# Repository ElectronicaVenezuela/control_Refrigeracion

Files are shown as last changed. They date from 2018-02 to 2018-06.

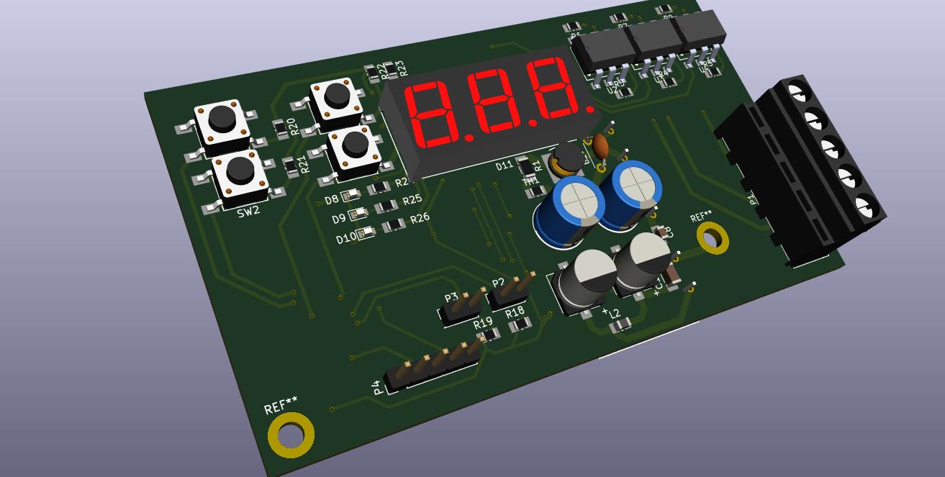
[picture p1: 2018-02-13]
Hartware_2.0.0/FABRICACION/D21_2550.jpg

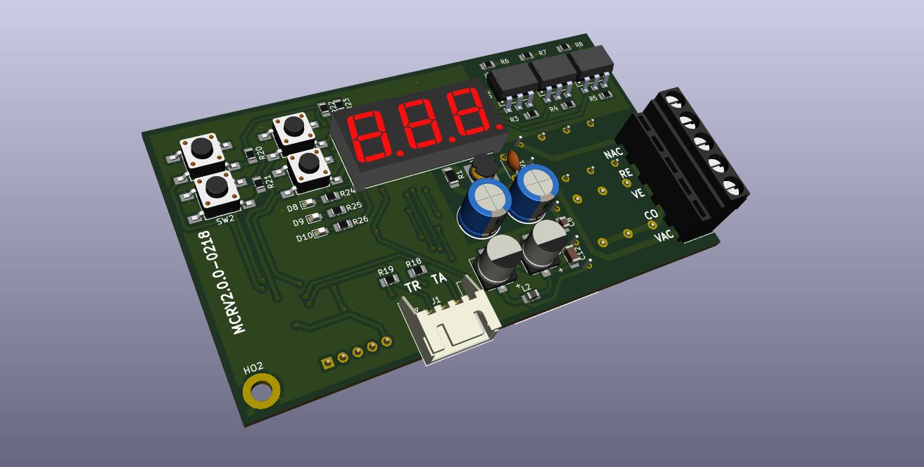
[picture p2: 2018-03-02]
Hartware_2.0.0/doc/D21_2550top.jpg

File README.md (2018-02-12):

# Módulo Control De Refrigeracion Comercial

Tesis para obtar al titulo de ingeniero de la Universidad Nacional Experimental del Táchira (UNET).

## Descripcion

Es un control de refrigeracion comercial con control de ciclos y deshielo, asi como tambien alertas contra posibles anomalias en el sistema de refrigeracion.

## Uso:

 - El hartware fue esta siendo desarrollado en [kicad version Nocturna](http://kicad-pcb.org/download/ubuntu/) para Ubuntu.

 - Las librerias usadas de componentes estan en: 
    -[Symbols](https://github.com/picli3/kicad-symbols.git)
    -[FootPrints](https://github.com/picli3/kicad-footprints.git)
    -[Packages3D](https://github.com/picli3/kicad-packages3D.git)
Se deben clonar y asociarse con el proyecto.

## Autor:

Maykol Rey Maykolrey@gmail.com

## Tutor:

Dr. Cesar contreras.

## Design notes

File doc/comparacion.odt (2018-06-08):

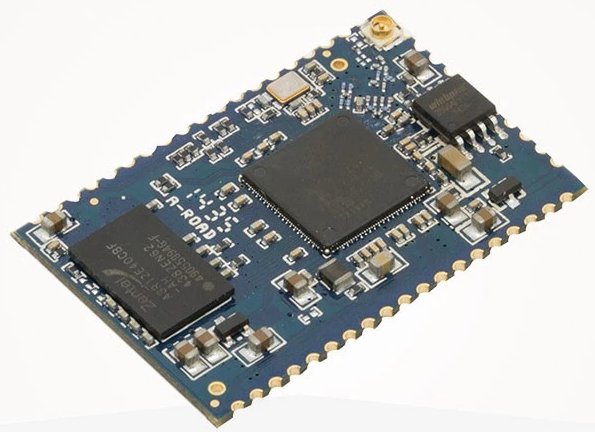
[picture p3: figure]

Comparación de procesadores

Skylab skw72 ar9331 Precio $10

Características

400MHz PCU

1. Conforme a IEEE 802.11b/G/n 1x1wlans

2. DDR2 memoria de hasta 512 MB

Memoria flash de hasta 64 MB

4.4lan puertos y 1 puerto WAN

5. UART de alta velocidad

Soporte técnico de 6. USB 2.0 modo de acogida

7. soporte AP/cliente/modo repetidor

8. soporte UART A WiFi transparente

9. Seguridad: WEP 64/128, WPA, WPA2, TKIP, AES, wapi

10. Conforme cumple los requisitos de medio ambiente

11.40.5 (l) x 27.5 (W) x 2.9 (h) mm Dimensión pequeña

Rasbberry pi zero $24

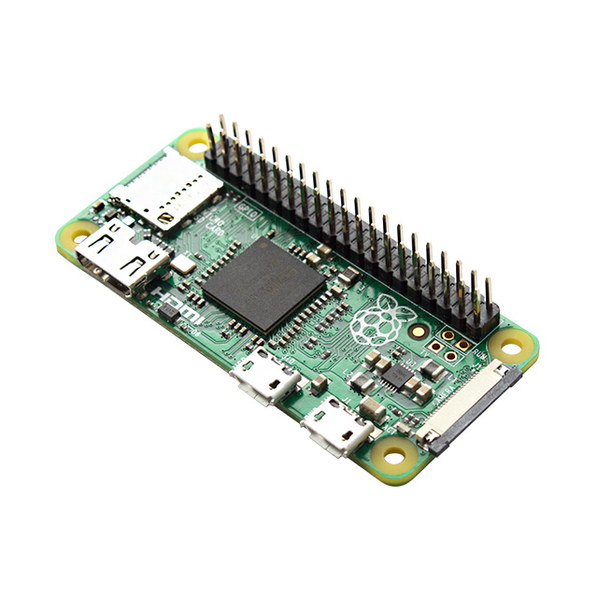
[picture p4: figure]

#### TECHNICAL SPECIFICATIONS

The Raspberry Pi Zero is half the size of a Model A+, with twice the utility. A tiny Raspberry Pi that’s affordable enough for any project!

- 1GHz single-core CPU
- 512MB RAM
- Mini HDMI port
- Micro USB OTG port
- Micro USB power
- HAT-compatible 40-pin header
- Composite video and reset headers
- CSI camera connector (v1.3 only)

### The Omega2 at a Glance $9

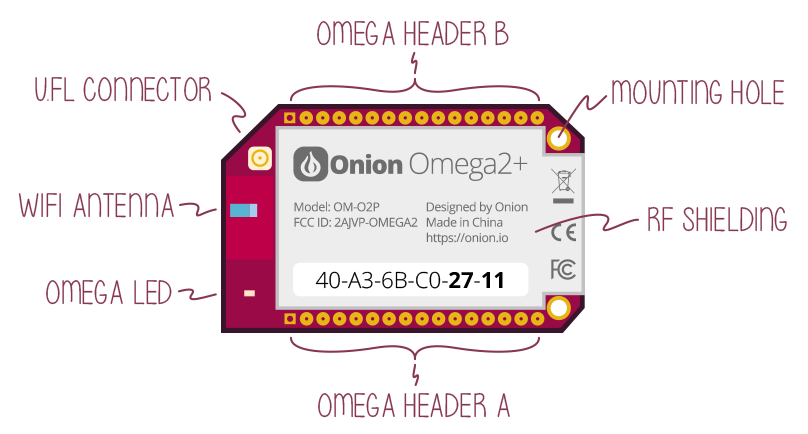
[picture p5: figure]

Omega2+ Specs
Processor | 580MHz MIPS CPU
Memory | 128MB Memory
Storage | 32MB Storage
USB | USB 2.0
MicroSD Slot | Yes
WiFi adapter | b/g/n Wi-Fi
GPIOs | 15
PWM | 2
UART | 2
I2C | 1
SPI | 1
I2S | 1

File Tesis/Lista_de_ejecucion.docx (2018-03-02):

Lista por completar para la tesis

1) fabricar placa a china

2) comprar componentes

3) ensamblar

4) probar algoritmo

5) hacer cubierta e imprimirla.

Documentar.

1) Realizar las cartas y tema el tema legal para realizar la tesis.

2) reestructurar los capitulos I,II y III con las nuevas condiciones.

3) Realizar todo el capitulo IV y V.

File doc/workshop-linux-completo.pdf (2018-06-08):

## Linux embebido

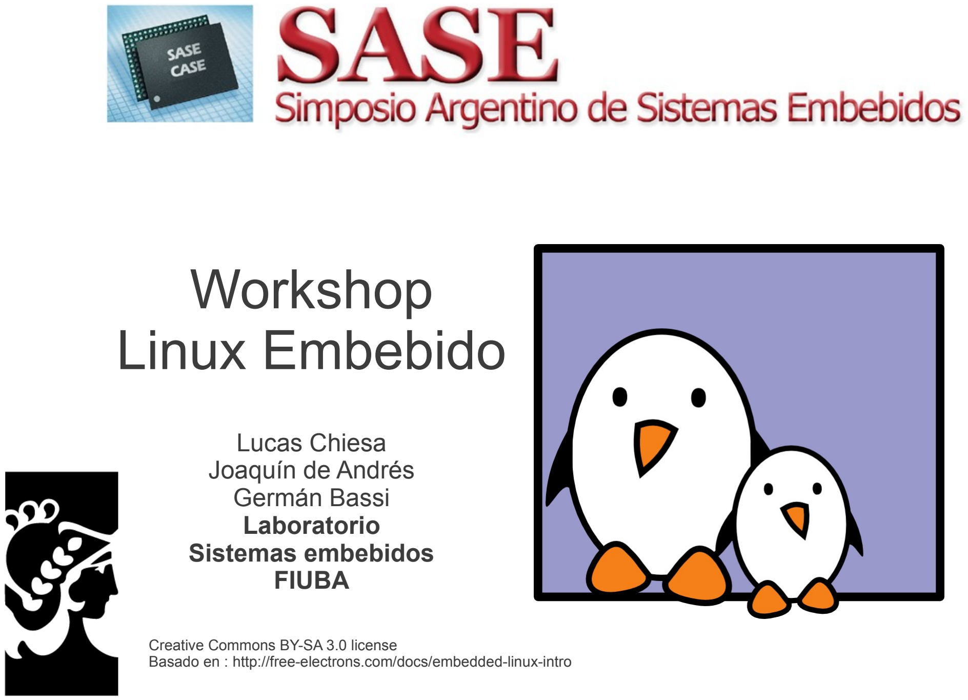
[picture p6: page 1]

## Workshop Linux Embebido

Lucas Chiesa
Joaquín de Andrés
Germán Bassi
Laboratorio
Sistemas embebidos
FIUBA

Creative Commons BY-SA 3.0 license
Basado en : http://free-electrons.com/docs/embedded-linux-intro

SASE 2012 Workshop Linux Embebido | 2

## ¿Sistema embebido?

Un sistema embebido o empotrado es un sistema de computación diseñado para realizar una o algunas pocas funciones dedicadas frecuentemente en un sistema de computación en tiempo real. Los sistemas embebidos se utilizan para usos muy diferentes a los usos generales a los que se suelen someter a las computadoras personales.

Wikipedia, http://es.wikipedia.org/wiki/Sistema_embebido

SASE 2012 Workshop Linux Embebido | 3

## Muchos sistemas diferentes

Es una definición muy genérica:
Cubre muchos tipos diferentes de sistemas
Línea borrosa con sistemas tradicionales
Productos “Consumer Electronics (CE)”:
Routers hogareños, reproductores de DVD, Televisores, cámaras digitales, GPS, celulares ...
Productos industriales:
Controladores de máquinas, alarmas, equipos de vigilancia, autos, satélites...

## Muchos productos diferentes

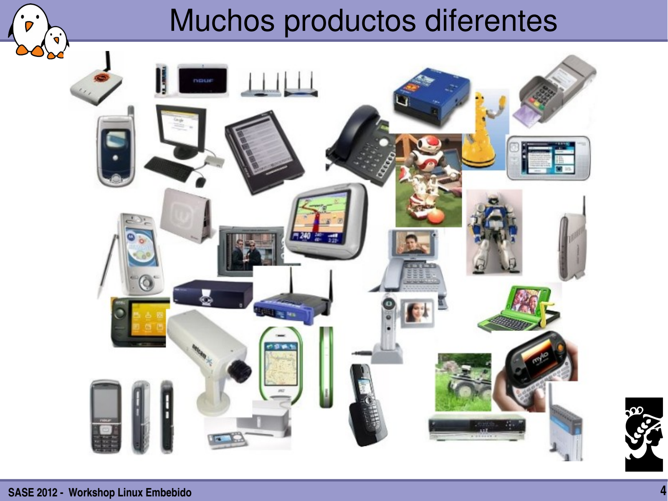
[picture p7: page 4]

SASE 2012 Workshop Linux Embebido | 4

SASE 2012 Workshop Linux Embebido | 5

## Linux embebido

El Software Libre y Abierto ofrece una rango muy amplio de herramientas para desarrollar sistemas embebidos. Ventajas
- Reutilizar componentes existentes para el sistema base. Permite concentrarse en el valor agregado del producto.
- Componentes de alta calidad y muy probados. (Kernel Linux , librerías de C ...)
- Control completo sobre la elección de componentes. Modificaciones posibles ilimitadas.
- Soporte por la comunidades: tutoriales, listas de correo...
- Bajo costo, sin licencias por unidad.
- Acceso más simple al software y a las herramientas.

SASE 2012 Workshop Linux Embebido | 6

## Ejemplos de dispositivos

GPS: TomTom y Garmin
Routers hogareños: Linksys, Netgear PDA: Zaurus, Nokia N8x0
TVs, DVDs: Sony, Philips, ...
Celulares: Motorola, Android, OpenMoko
Y muchos productos que uno no se imagina...

SASE 2012 Workshop Linux Embebido | 7

## Arquitectura global

Hardware

Bootloader

Kernel Linux

Librería de C

Librería | Librería | Librería
Aplicación | Aplicación
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
SASE 2012 Workshop Linux Embebido | 8

## Hardware embebido

El hardware para sistemas embebidos es usualmente diferente de los sistemas comunes.
- Normalmente usan otras arquitecturas:
ARM, MIPS o PowerPC. x86 también es usado.
- Almacenamiento flash (NOR o NAND), usualmente con capacidad limitada. (de pocos MB a cientos de MB)
- Capacidad de RAM limitada (desde unos pocos MB)
- Muchos buses de conexión no comunes en desktops: I2C, SPI, 1-wire, CAN, etc.
Placas de desarrollo por cientos de dolares
- Usualmente usadas como base de nuestro diseño.

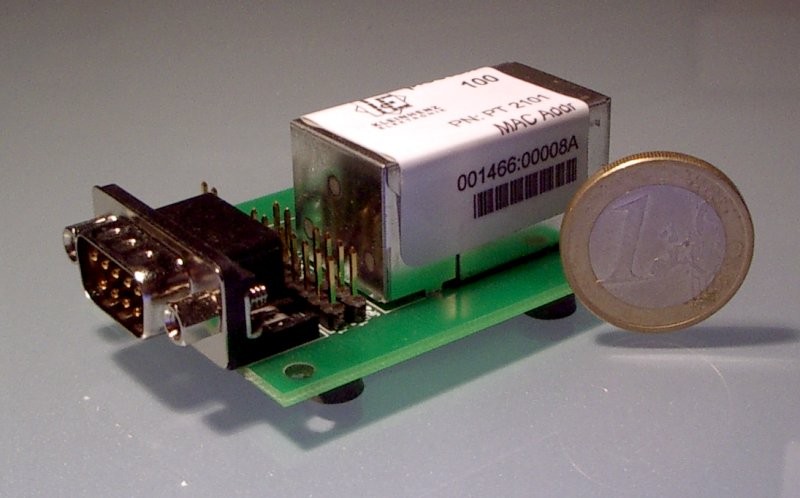
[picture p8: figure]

SASE 2012 Workshop Linux Embebido | 9

## Ejemplos

Picotux 100
ARM7 55 MHz, Netsilicon
NS7520
2 MB de flash
8 MB de RAM
Ethernet
5 GPIOs
Serial

BeagleBoard C4
Cortex A8 750 MHz, TI
OMAP 3550
256 MB de RAM
256 MB de NAND flash
DVI, audio entrada y salida, USB, etc

SASE 2012 Workshop Linux Embebido | 10

## Requerimientos mínimos

Una CPU soportada por el GCC y el Kernel Linux
- 32 bit CPU
- CPUs sin MMU son soportadas por uClinux, que no vamos a ver ahora.
Unos MB de RAM, desde 4 MB.
8 MB para hacer algo útil.
Unos pocos MB de almacenamiento, desde 2 MB.
4 MB para hacer algo útil.
Linux no está diseñado para procesadores con KBs de RAM o ROM:
- Se usan sin SO.
- Sistemas reducidos, como FreeRTOS

SASE 2012 Workshop Linux Embebido | 11

## Componentes de software

Crosscompilation toolchain
- Compilador que se ejecuta en una computadora de desarrollo y genera binarios para el destino.
Bootloader
- Iniciado por el hardware, es el responsable de la inicialización básica y ejecutar el Kernel.
Kernel Linux
- Contiene el administrador de procesos y memoria, stack de red, controladores de dispositivos, provee servicios a las aplicaciones. Librería de C
- Interfaz entre el Kernel y las aplicaciones de usuario.
Librerías y aplicaciones
- Propias o producidas por otros.

SASE 2012 Workshop Linux Embebido | 12

## Armado de un sistema Linux

Se necesitan realizar diferentes tareas para producir un sistema Linux embebido:
Desarrollo del Board Support Package
- Un BSP contiene el bootloader y Kernel con los drivers necesarios para mi hardware destino.
- No es donde nos vamos a centrar.
Integración del sistema
- Integrar todos los componentes, BSP, librerías y aplicaciones utilizadas y las aplicaciones propias para obtener un sistema funcional.
- Propósito de este curso.
Desarrollo de aplicaciones
- Aplicaciones normales de Linux, pero usando librerías especiales.

SASE 2012 Workshop Linux Embebido | 13

## Root filesystem

En un sistema Linux, los sistemas de archivos se “montan” dentro de una jerarquía global de directorios y archivos.
Un sistema particular, el root, se monta como el directorio /.
En sistemas embebidos, este sistema de archivos contiene todos los archivos del sistema.
Por lo tanto, crearlo es una de las tareas principales de la integración de componentes.
El Kernel normalmente se mantiene separado.

Bootloader

Kernel

Root
filesystem

Contenidos de
la Flash

SASE 2012 Workshop Linux Embebido | 14

## Entorno de desarrollo

Dos maneras de desarrollar un sistema Linux:
- Usar soluciones provistas y soportadas por empresas como MontaVista, Wind River o TimeSys. Cada una tiene sus herramientas propias.
- Usar herramientas provistas por la comunidad.
No vamos a promover ninguna empresa en particular, por lo que vamos a usar herramientas de la comunidad.
- Lo importante es entender los conceptos, migrar de herramienta siempre es más fácil.
Desarrollar un sistema Linux requiere usar Linux.
- Las herramientas comunitarias no están disponibles para otras plataformas.
- Entender Linux en el desktop nos va a facilitar el desarrollo de Linux embebido.

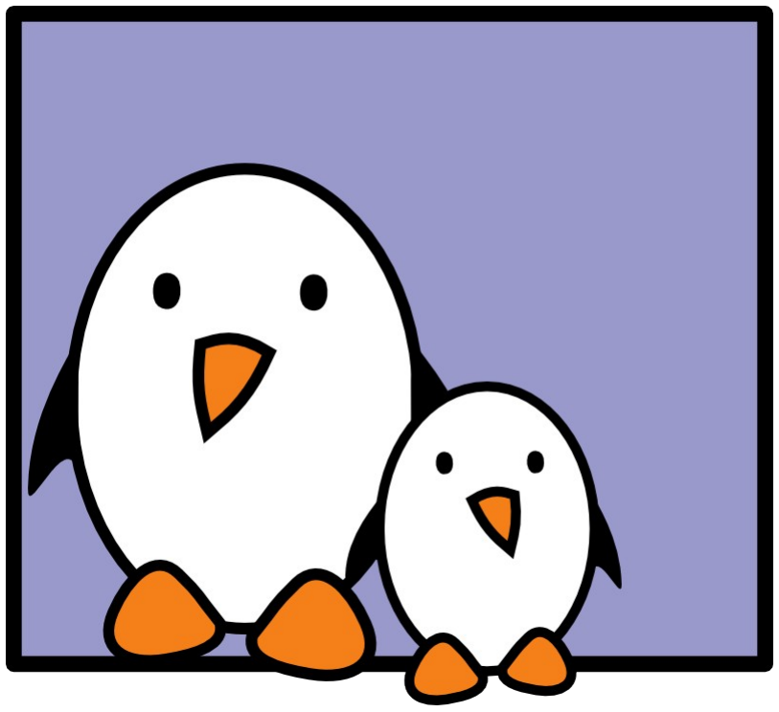
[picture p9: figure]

SASE 2012 Workshop Linux Embebido | 15

## Linux embebido

# Uso de un sistema Linux

SASE 2012 Workshop Linux Embebido | 16

## Uso de un sistema Linux

## Sistema de archivos y dispositivos

SASE 2012 Workshop Linux Embebido | 17

## Creando un sistema de archivos

Ejemplos
mkfs.ext2 /dev/sda1
Formatea la partición /dev/sda1 en formato ext2. mkfs.ext2 -F disk.img
Formatea una imagen de disco en ext2
mkfs.vfat v -F 32 /dev/sda1 (v: verbose) Formatea la misma partición anterior en FAT32.
mkfs.vfat v -F 32 disk.img
Formatea la imagen en FAT32.
Imágenes de discos en blanco se pueden crear así: (archivo de 64 MB): dd if=/dev/zero of=disk.img bs=1M count=64

-F: force. Ejecuta aunque no sea un dispositivo real.

SASE 2012 Workshop Linux Embebido | 18

## Montando un dispositivo

Para hacer cualquier sistema de archivos visible en el sistema hay que montarlos.
La primera vez, se crea el punto de montaje: mkdir /mnt/usbdisk (ejemplo)
Ahora lo montamos:
mount t vfat /dev/sda1 /mnt/usbdisk /dev/sda1: dispositivo físico
t: especifica el formato del sistema de archivo (ext2, ext3, vfat, reiserfs, iso9660...)

Datos
crudos

mount

Estructura
de
directorios

SASE 2012 Workshop Linux Embebido | 19

## Montando un dispositivo

También se puede montar una imagen de un sistema de archivos guardada en un archivo regular (loop devices)
Muy útil para desarrollar y probar un sistema de archivos que estamos armando para otra computadora.
Útil para acceder a los contenidos de una imagen de CD (iso) sin tener que grabar el disco.
Ejemplo:
mount o loop t vfat usbkey.img /mnt/usbdisk

SASE 2012 Workshop Linux Embebido | 20

## Listando dispositivos montados

Usando el comando mount sin argumentos se obtiene la lista:
/dev/hda6 on / type ext3 (rw,noatime)
none on /proc type proc (rw,noatime)
none on /sys type sysfs (rw)
none on /dev/pts type devpts (rw,gid=5,mode=620) usbfs on /proc/bus/usb type usbfs (rw) /dev/hda4 on /data type ext3 (rw,noatime)
none on /dev/shm type tmpfs (rw)
/dev/hda1 on /win type vfat (rw,uid=501,gid=501) none on /proc/sys/fs/binfmt_misc type binfmt_misc (rw)

SASE 2012 Workshop Linux Embebido | 21

## Desmontando dispositivos

umount /mnt/usbdisk
Termina todas las transacciones pendientes en el dispositivo y lo desmonta.
Para poder desmontar un dispositivo hay que cerrar todos sus archivos abiertos:
- Cerrar todos los programas que usen algún archivo del directorio montado.
- Estar seguro que ningún shell esté abierto en esa partición.
- Se puede usar el comando lsof <mount point> (list open files) para ver todos los archivos abiertos en ese directorio.

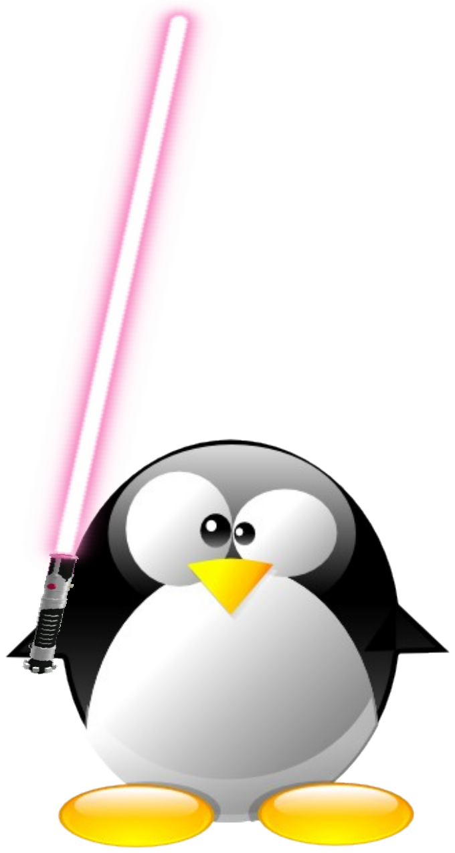
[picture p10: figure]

SASE 2012 Workshop Linux Embebido | 22

## El lado oscuro de root

root: Se necesitan sus privilegios sólo para operaciones específicas, con impacto en la seguridad. Por ejemplo: montar, crear dispositivos, cargar drivers, configurando la red,
cambiar permisos, instalar paquetes...
Por más que uno tenga la clave de root, la cuenta normal tiene que ser suficiente para el 99.9% de las actividades (a menos que seas el sysadmin)
En este curso es aceptable que usen root.
En la vida real, pueden no tener esta cuenta disponible.

SASE 2012 Workshop Linux Embebido | 23

## Usando la cuenta root

En caso que uno realmente quiera ser root...
Si uno tiene el password de root:
su (switch user)
En distribuciones modernas, el comando sudo te da acceso a algunos privilegios de root usando la clave de tu usuario.
Ejemplo: sudo mount /dev/hda4 /home

SASE 2012 Workshop Linux Embebido | 24

## Administración básica del sistema

## Manejo de paquetes

SASE 2012 Workshop Linux Embebido | 25

## Paquetes de software

La forma de distribuir software en GNU/Linux difiere de la que se usa en Windows.
Las distribuciones de Linux proveen una forma central y coherente de instalar, actualizar y borrar aplicaciones y librerías: Paquetes.
Los paquetes contienen la aplicación, las librerías e información extra, como la versión y las dependencias.
- .deb en Debian y Ubuntu, .rpm en Mandriva, Fedora, OpenSUSE Los paquetes se guardan en repositorios, usualmente servers HTTP o FTP.
Siempre hay que usar paquetes oficiales de la distribución, a menos que sea estrictamente necesario.

SASE 2012 Workshop Linux Embebido | 26

## Manejando paquetes de software

Instrucciones para sistemas basados en Debian GNU/Linux: (Debian, Ubuntu...)
Los repositorios de paquetes se especifican en: /etc/apt/sources.list
Para actualizar la lista de paquetes:
sudo aptget update
Para encontrar un paquete para instalar, se pueden usar los buscadores web: http://packages.debian.org o http://packages.ubuntu.com. También se puede usar: aptcache search <keyword>

SASE 2012 Workshop Linux Embebido | 27

## Manejando paquetes de software

Para instalar un paquete:
sudo aptget install <package> Para desinstalar un paquete:
sudo aptget remove <package> Para aplicar todas las actualizaciones: sudo aptget distupgrade
Para obtener información de un paquete: sudo aptcache show <package> Existen interfaces gráficas:
- Synaptic para GNOME
- Adept para KDE
Para más información sobre administración de paquetes: http://www.debian.org/doc/manuals/apthowto/ (http://www.debian.org/doc/manuals/apt-howto/)

SASE 2012 Workshop Linux Embebido | 28

## Apagando el sistema

halt
Apaga inmediatamente el sistema. reboot
Reinicia inmediatamente el sistema.
[Ctrl][Alt][Del]
También funciona el GNU/Linux para reiniciar.
Sistemas embebidos: hay que usar un init y especificar una combinación de teclas en /etc/inittab.

## Práctica – Usando Linux

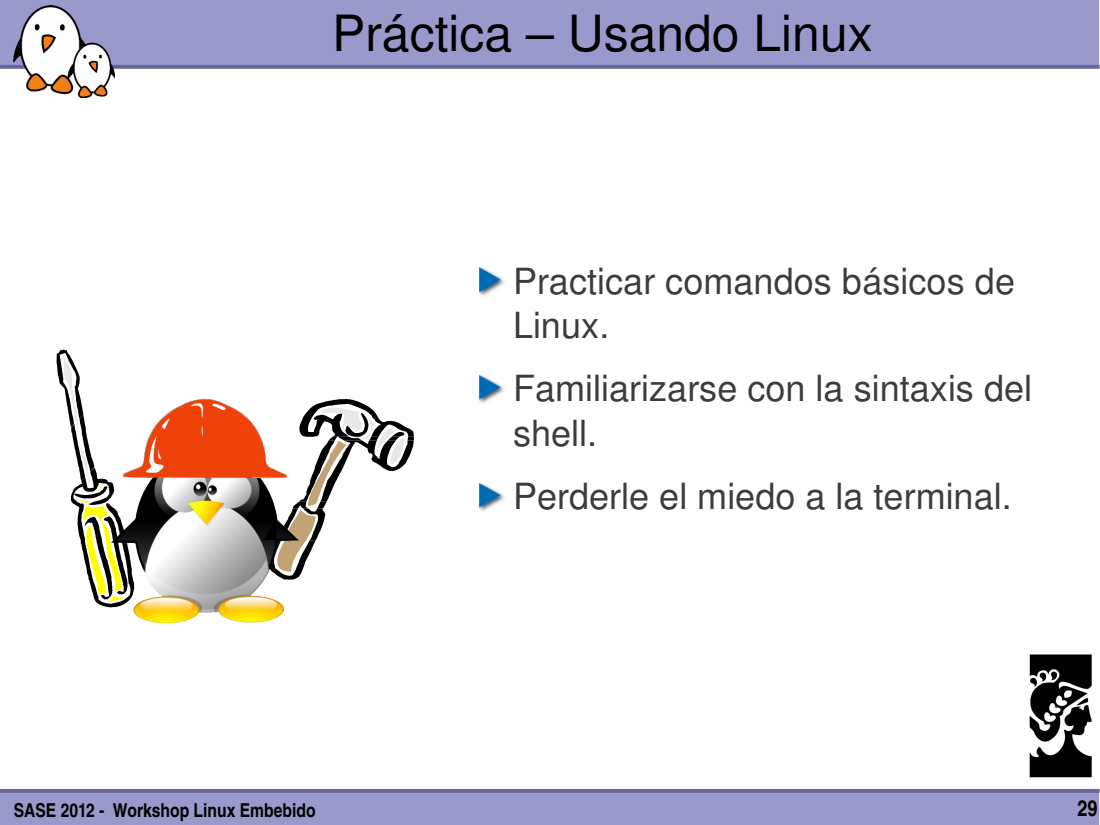
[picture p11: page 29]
SASE 2012 Workshop Linux Embebido

Practicar comandos básicos de
Linux.
Familiarizarse con la sintaxis del
shell.
Perderle el miedo a la terminal.

SASE 2012 Workshop Linux Embebido | 30

## Sistemas embebidos

# Introducción al Kernel Linux

SASE 2012 Workshop Linux Embebido | 31

## Desarrollo de Linux Embebido

## Presentando el kernel

Características de Linux

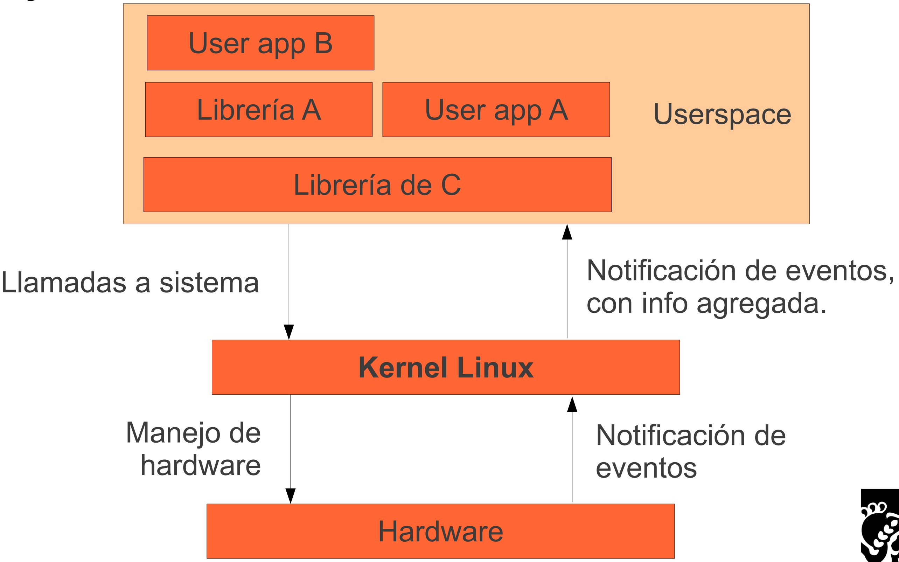
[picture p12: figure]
Userspace; Librería de C; Kernel Linux; Hardware; Librería A; User app A; User app B; Notificación de eventos, con info agregada. Llamadas a sistema; Notificación de eventos; Manejo de hardware

SASE 2012 Workshop Linux Embebido | 32

## Kernel Linux en el sistema

SASE 2012 Workshop Linux Embebido | 33

## Historia

El Kernel Linux es un componente del sistema, requiere librerías y aplicaciones para proveer funcionalidad a los usuarios finales. Creado por un estudiante finlandes, Linus Torvalds, como un hobby en 1991.
- Rápidamente fue adoptado como el Kernel para formar un sistema operativo libre.
Linus Torvalds fue capaz de crear una comunidad de usuarios y programadores grande y dinámica alrededor de Linux. Actualmente cientos de personas contribuyen a cada release del Kernel, tanto individuos particulares como pertenecientes a grandes empresas.

SASE 2012 Workshop Linux Embebido | 34

## Licencia de Linux

Todas las fuentes del Kernel son software libre, liberado bajo la licencia GNU General Public License version 2 (GPL v2).
Para el Kernel, esto implica que:
- Cuando uno recibe o compra un dispositivo con Linux dentro, debe recibir las fuentes de Linux, con todos los derechos de estudiar modificar y redistribuir.
- Cuando uno produce equipos basados en Linux, uno debe dar las fuentes al destinatario, sin restricciones. Más adelante vamos a ver en detalle las licencias libres.

SASE 2012 Workshop Linux Embebido | 35

## Características principales

Portabilidad y soporte de
hardware. Corre en la
mayoría de las arquitecturas. Escalabilidad.
Funciona en super
computadoras como en
pequeños dispositivos.
(4 MB de RAM es suficiente). Cumple con estándares de
interoperatividad
Muy completo y robusto
soporte de red.

Seguridad
No puede ocultar las fallas. El código es revisado por muchos expertos.
Estable y confiable.
Modular. Puede incluir sólo lo que nuestro sistema necesita. Fácil de programar. Se puede aprender de código existente. Muchos recursos en Internet

SASE 2012 Workshop Linux Embebido | 36

## Arquitecturas soportadas

Para el Kernel 2.6.31
Revisar el directorio arch/ (http://lxr.free-electrons.com/source/arch/) en las fuentes.
Requerimiento mínimo: 32 bits, con o sin MMU, y soporte de gcc. Arquitecturas de 32 bits
arm, (http://lxr.free-electrons.com/source/arch/arm/) avr32, (http://lxr.free-electrons.com/source/arch/avr32/) blackfin, (http://lxr.free-electrons.com/source/arch/blackfin/) cris, (http://lxr.free-electrons.com/source/arch/cris/) frv, (http://lxr.free-electrons.com/source/arch/frv/) h8300, (http://lxr.free-electrons.com/source/arch/h8300/) m32r, (http://lxr.free-electrons.com/source/arch/m32r/) m68k, (http://lxr.free-electrons.com/source/arch/m68k/) m68knommu, (http://lxr.free-electrons.com/source/arch/m68knommu/) microblaze, (http://lxr.free-electrons.com/source/arch/microblaze/) mips, (http://lxr.free-electrons.com/source/arch/mips/) mn10300, (http://lxr.free-electrons.com/source/arch/mn10300/) parisc, (http://lxr.free-electrons.com/source/arch/parisc/) s390, (http://lxr.free-electrons.com/source/arch/s390/) sparc, (http://lxr.free-electrons.com/source/arch/sparc/) um, (http://lxr.free-electrons.com/source/arch/um/) xtensa (http://lxr.free-electrons.com/source/arch/xtensa/)
Arquitecturas de 64 bits:
alpha, (http://lxr.free-electrons.com/source/arch/alpha/) ia64, (http://lxr.free-electrons.com/source/arch/ia64/) sparc64 (http://lxr.free-electrons.com/source/arch/sparc64/)
Arquitecturas de 32 o 64 bits:
powerpc, (http://lxr.free-electrons.com/source/arch/powerpc/) x86, (http://lxr.free-electrons.com/source/arch/x86/) sh (http://lxr.free-electrons.com/source/arch/s390/)
Más detalles en: arch/<arch>/Kconfig, arch/<arch>/README, o Documentation/<arch>/

SASE 2012 Workshop Linux Embebido | 37

## Llamadas a sistema

La principal interfaz entre el Kernel y userspace es un conjunto de llamadas a sistema.
Existen ~300 llamadas a sistemas que proveen los servicios principales del Kernel
- Operaciones en archivos y dispositivos, operaciones de red, comunicación entre procesos, administración de procesos, manejo de memoria, timers, threads, sincronización, etc.
Interfaz estable en el tiempo: sólo se pueden agregar nuevas llamadas.
La interfaz a las llamadas al sistema es abstraída por la librería de C. Los programas de userspace usualmente no hacen llamadas al sistema, usan las funciones correspondiente de la librería.

SASE 2012 Workshop Linux Embebido | 38

## Sistemas de archivos virtuales

Linux ofrece información del sistema y el Kernel a userspace mediante sistemas de archivos virtuales (virtuales: no existen en un ningún almacenamiento real). No se necesita saber programar para acceder a esta información!
Montar /proc:
sudo mount t proc none /proc
Montar /sys:
sudo mount t sysfs none /sys
Tipo de fs | Dispositivo o imagen de fs En el caso de un fs virtual cualquier texto es válido
Lugar de montaje

SASE 2012 Workshop Linux Embebido | 39

## Detalles de /proc

Algunos ejemplos:
/proc/cpuinfo: información del procesador /proc/meminfo: estado de la memoria
/proc/version: información de compilación y versión del kernel
/proc/cmdline: línea de comando del Kernel /proc/<pid>/environ: entorno de ejecución /proc/<pid>/cmdline: linea de comando del proceso ... y mucho más! Véalo con sus propios ojos!
Muchos detalles acerca de /proc disponibles en: Documentation/filesystems/proc.txt (http://free-electrons.com/kerneldoc/latest/filesystems/proc.txt)
(casi 2000 líneas) en las fuentes del Kernel.

SASE 2012 Workshop Linux Embebido | 40

## Desarrollo de Linux Embebido

## Kernel Linux

Esquema de versiones y modelo de desarrollo

SASE 2012 Workshop Linux Embebido | 41

## Hasta 2.6

Una nueva rama estable cada 2 o 3 años
- Identificada por un número par en el medio
- Ejemplos: 1.0, 2.0, 2.2, 2.4
Una rama de desarrollo para integrar nueva funcionalidad y cambios mayores
- Identificada por un número impar en el medio
- Ejemplos: 2.1, 2.3, 2.5
- Después de un tiempo, la rama de desarrollo pasaba a ser la base de una rama estable.
Versiones menores de vez en cuando: 2.2.23, 2.5.12, etc.

SASE 2012 Workshop Linux Embebido | 42

## Hasta 2.6

2.4.0 | 2.4.1 | 2.4.2 | 2.4.3 | 2.4.4 | 2.4.5 | 2.4.6 | 2.4.7 | 2.4.8
2.5.0 2.5.1 2.5.2 2.5.3 2.5.4 | 2.6.0 2.6.1

Versión estable

Desarrollo | Estable

Nota: En realidad existen muchas más versiones menores en cada rama.

SASE 2012 Workshop Linux Embebido | 43

## Cambios desde Linux 2.6

Desde 2.6.0, los programadores pudieron agregar muchas nuevas funciones de a una a paso constante sin tener que hacer grandes cambios en los subsistemas existentes. Abrir una nueva rama de desarrollo Linux 2.7 (o 2.9) va a ser necesario cuando Linux 2.6 no pueda acomodar más funciones importantes sin cambios muy grandes.
Gracias a esto, muchas nuevas funciones llegan a los usuarios a un paso mucho más rápido.

SASE 2012 Workshop Linux Embebido | 44

## Cambios desde Linux 2.6

Desde 2.6.14, los programadores del Kernel se pusieron de acuerdo en el siguiente modelo de desarrollo:
Después de un release de una versión 2.6.x, se abre una ventana de 2 semanas para merge durante la cual los principales cambios son aplicados.
Se cierra la ventana de merge con el release de la versión 2.6.(x+1)rc1
Se abre el período para arreglar bugs, de 6 a 10 semanas.
En intervalos regulares durante el período de arreglo de bugs se liberan las versiones de prueba 2.6.(x+1)rcY.
Cuando se lo considera suficientemente estable,
el Kernel 2.6.(x+1) es liberado, y el proceso vuelve a comenzar.

SASE 2012 Workshop Linux Embebido | 45

## Ventanas de merge y arreglos

Ventana de merge | Arreglar bugs
2.6.21 | 2.6.22-rc1

2.6.22-rc2

2.6.22-rc3 | 2.6.22-rc5
2.6.22-rc4 | 2.6.22
2 semanas | 6 a 10 semanas
2.6.21.1 2.6.21.2 | 2.6.21.3 2.6.21.4 | 2.6.21.5

Actualizaciones con
arreglos de bugs
| | 2.6.22.1

SASE 2012 Workshop Linux Embebido | 46

## Más estabilidad con kernel 2.6

Problema: los arreglos de bugs y seguridad se hacen sólo en la versión más nueva (a lo sumo dos anteriores). Las distribuciones, por supuesto, las aplican en los kernels que están usando.
Algunas personas necesitan tener un Kernel nuevo pero con soporte por un plazo prolongado.
Se puede tener soporte de largo plazo de los proveedores de Linux embebido.
Se puede reutilizar las fuentes del Kernel de las versiones de Ubuntu LTS, o Debian (5 o 3 años de updates gratis). Algunas versiones se mantienen por un tiempo prolongado por kernel.org (Linux 2.6.27 por ejemplo).

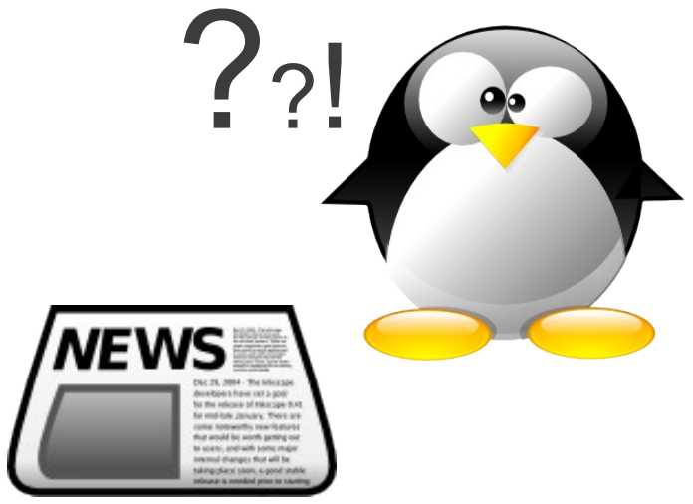
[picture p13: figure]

SASE 2012 Workshop Linux Embebido | 47

## ¿Qué tiene de nuevo cada versión?

¡¡El changelog oficial de cada versión es simplemente una larga lista de parches individuales!!
Muy difícil de saber cuáles son los cambios claves y tener una vista global de los cambios.
Afortunadamente, un resumen de los cambios fundamentales (con suficiente detalle) se encuentra en: http://wiki.kernelnewbies.org/LinuxChanges

commit 3c92c2ba33cd7d666c5f83cc32aa590e794e91b0 Author: Andi Kleen <ak@suse.de>
Date: Tue Oct 11 01:28:33 2005 +0200

[PATCH] i386: Don't discard upper 32bits of HWCR on K8

Need to use long long, not long when RMWing a MSR. I think it's harmless right now, but still should be better fixed
if AMD adds any bits in the upper 32bit of HWCR.

Bug was introduced with the TLB flush filter fix for i386

Signed-off-by: Andi Kleen <ak@suse.de> Signed-off-by: Linus Torvalds <torvalds@osdl.org> ...

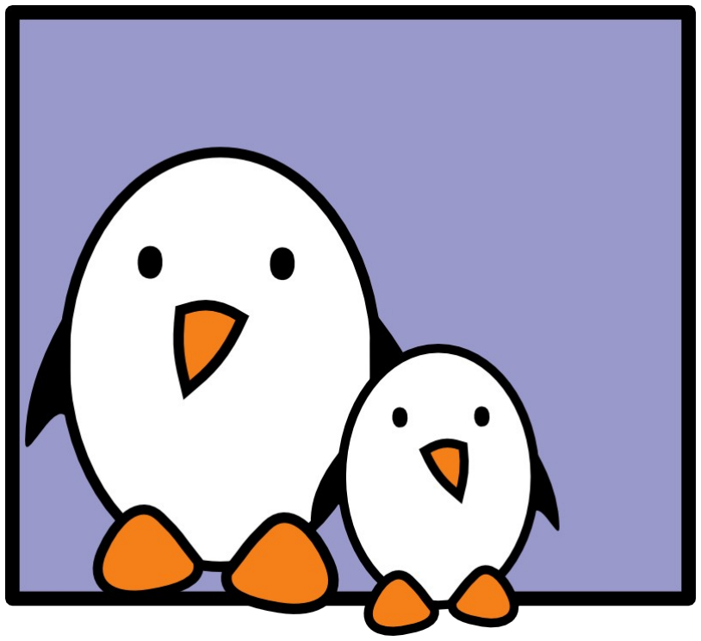
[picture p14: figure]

SASE 2012 Workshop Linux Embebido | 48

## Desarrollo de sistemas Linux

# Crosscompiling toolchains

SASE 2012 Workshop Linux Embebido | 49

## Definición

Las herramientas de desarrollo que uno tiene normalmente en un desktop se llaman toolchain nativo.
Este toolchain corre en el desktop y genera código para el desktop. Usualmente x86.
Para sistemas embebidos usualmente no se puede o no es deseable.
- El target tiene recursos limitados (poca RAM y almacenamiento)
- El target es mucho más lento que el desktop.
- Uno puede no querer tener instalados las herramientas de desarrollo en el target.
Por lo tanto, generalmente se usan crosscompiling toolchains. Corren en el desktop y general código para el target.

SASE 2012 Workshop Linux Embebido | 50

## Definición

x86

x86 | ARM

Máquina que
compila

Máquina
que ejecuta

Código fuente

Toolchain nativo | Cross-compiling toolchain
Binario x86 | Binario ARM

SASE 2012 Workshop Linux Embebido | 51

## Componentes

Binutils | Kernel headers
Librerías de C/C++ | Compilador GCC

GDB debugger
(opcional)

SASE 2012 Workshop Linux Embebido | 52

## Binutils

Binutils es un conjunto de herramientas para manipular binarios de una determinada arquitectura:
- as, el ensamblador, genera código binario a partir de código assembler
- ld, el linker
- ar, ranlib, genera archivos .a, usados para librerías.
- objdump, readelf, size, nm, strings, para inspeccionar binarios. Herramientas de análisis muy útiles!
- strip, remueve partes de los binarios que no se usan. http://www.gnu.org/software/binutils/
Licencia GPL

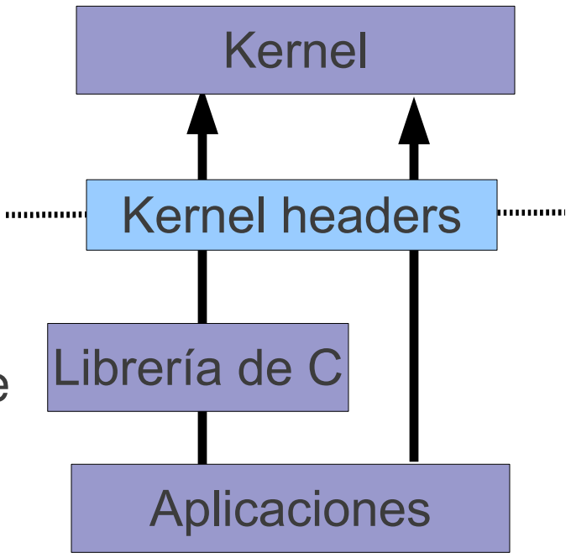
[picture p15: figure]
Kernel; Kernel headers; Librería de C; Aplicaciones

SASE 2012 Workshop Linux Embebido | 53

## Kernel headers

La librería de C y los programas tienen que interactuar con el Kernel
- Llamadas a sistema disponibles.
- Definiciones de constantes.
- Estructura de datos, etc.
Por lo tanto, para compilar la librería de
C se necesitan los Kernel headers, y muchas aplicaciones también.

Disponibles dentro de las fuentes del Kernel

SASE 2012 Workshop Linux Embebido | 54

## Kernel headers

La ABI kerneltouserspace es compatible hacia atrás:
- Binarios generados con un toolchain usando headers anteriores que el Kernel que se está usando, van a funcionar pero no van a poder usar las prestaciones nuevas.
- Binarios compilados contra headers más nuevos que el Kernel en uso pueden romperse si se usan características no presentes en el Kernel viejo.
- No es necesario usar los headers más nuevos, salvo que se necesiten las últimas características.
Los headers se extraen de las fuentes del Kernel con el
comando make headers_install.

SASE 2012 Workshop Linux Embebido | 55

## Compilador GCC

Famoso compilador libre GCC
Puede compilar C, C++, Ada, Fortran, Java, Objective-C, Objective-C++, y generar código para muchas arquitecturas, incluyendo ARM, AVR, AVR32, Blackfin, CRIS, FRV, M32, MIPS, MN10300, PowerPC, SH, v850, i386, x86_64, IA64, Xtensa, etc. http://gcc.gnu.org/
Disponible bajo licencia GPL.
Las librerías que utiliza son LGPL.

SASE 2012 Workshop Linux Embebido | 56

## Librería de C

La librería de C es un componente esencial de una instalación de Linux.
- Interfaz entre las aplicaciones y el Kernel.
- Provee una API de C muy conocida para facilitar el desarrollo de aplicaciones. Existen muchas librerías de C:
glibc, uClibc, eglibc, dietlibc, newlib, etc.
La elección de una librería se debe hacer en el momento de generar el toolchain, ya que el GCC se compila contra la librería.

Kernel

Librería de C

Aplicaciones

SASE 2012 Workshop Linux Embebido | 57

## glibc

http://www.gnu.org/software/libc/
Licencia: LGPL
Librería de C del proyecto GNU.
Diseñada para desempeño, respetar estándares y portabilidad.
Encontrada en casi todos los sistemas GNU / Linux. Por supuesto, mantenida activamente.
Bastante grande para sistemas embebidos: ~ 2.5 MB en arm (version 2.9 libc: 1.5 MB, libm: 750 KB)

SASE 2012 Workshop Linux Embebido | 58

## uClibc

http://www.uclibc.org/ de CodePoet Consulting
Licencia: LGPL
Librería de C pequeña, para sistemas embebidos:
- Muchas opciones de configuración: muchas funciones se pueden activar y desactivar usando la interfaz menuconfig.
- Funciona en Linux/uClinux, en la mayoría de las plataformas embebidas.
- No tiene una ABI estable, depende de la configuración de la librería.
- Se ocupa del tamaño antes que del desempeño.
- Se compila rápido.

SASE 2012 Workshop Linux Embebido | 59

## uClibc

La mayoría de las aplicaciones compilan contra uClibc, y todas las que se usan en embebidos.
Tamaño (arm): 4 veces más chica que glibc!
uClibc 0.9.30.1: ~ 600 KB (libuClibc: 460 KB, libm: 96KB) glibc 2.9: ~ 2.5 MB (para recordar)
Usada en una gran cantidad de dispositivos embebidos, incluidos muchos de “consumer electronics”.
Activamente soportada, gran base de usuarios.
Ahora soportada por MontaVista, TimeSys y Wind River.

SASE 2012 Workshop Linux Embebido | 60

## Querida encojí a los programas

Programa | Usando librerías compartidas | Compilado estático
| glibc | uClibc | glibc | uClibc
Plain “hello world” (stripped) | 5.6 K (glibc 2.9) | 5.4 K (uClibc 0.9.30.1) | 472 K (glibc 2.9) | 18 K (uClibc 0.9.30.1)
Busybox (stripped) | 245 K (older glibc) | 231 K (older uClibc) | 843 K (older glibc) | 311 K (older uClibc)

Comparación de tamaños de ejecutables en ARM

SASE 2012 Workshop Linux Embebido | 61

## eglibc

« Embedded glibc », LGPL
Variante de la GNU C Library (GLIBC) diseñada para funcionar en sistemas embebidos.
Compatible (fuente y binarios) con GLIBC
Sus objetivos incluyen tamaño reducido, componentes configurables, mejor soporte para crosscompilación.
Se puede compilar sin soporte par IPv6, localizaciones y muchas otras funciones.
Soportada por un consorcio, con Freescale, MIPS, MontaVista y Wind River como miembros.
Debian usa eglibc en todas las distribuciones. http://www.eglibc.org

SASE 2012 Workshop Linux Embebido | 62

## Otras librerías de C pequeñas

Existen otras librerías de C más pequeñas, pero ninguna con el objetivo de compilar una gran cantidad de aplicaciones existentes.
Requieren el código escrito especialmente para ellas. Opciones:
- Dietlibc, http://www.fefe.de/dietlibc/. Aproximadamente 70 KB.
- Newlib, http://sourceware.org/newlib/
- Klibc, http://www.kernel.org/pub/linux/libs/klibc/, diseñada para ser usada durante el booteo.

SASE 2012 Workshop Linux Embebido | 63

## Compilando el toolchain

Hay que diferenciar tres máquinas cuando se habla de la creación del toolchain:
- La máquina de compilación, donde el toolchain se compila.
- La máquina host, donde el toolchain se ejecuta.
- La máquina destino, donde se van a ejecutar los binarios generados por el toolchain.
Existen cuatro posibles maneras de crear el toolchain

SASE 2012 Workshop Linux Embebido | 64

## Compilando el toolchain

build | host | target

Nativo
toolchain normal en un desktop
build | host | target

Cross
Genera un toolchain que corre en el desktop y crea código para ejecutarlo en el target
build | host | target

Cross-nativo
Genera un toolchain que corre en el target y genera código para el target
build | host | target

Canadian
Un toolchain que se compila en el desktop, se ejecuta en un server y genera código para el target

La solución más común en embebidos

SASE 2012 Workshop Linux Embebido | 65

## Compilando el toolchain

Hay que tomar muchas decisiones al momento de hacer un toolchain.
- Elegir la librería de C
- Elegir la versión de los componentes que vamos a usar
Y la configuración de todas estas cosas.
- ¿Qué ABI debemos usar? Toolchains para ARM, pueden generar binarios usando la OABI (Old ABI) o la EABI (Embedded ABI), que son incompatibles.
- ¿Debe el toolchain soportar punto flotante por software?, ¿o el hardware provee soporte para estas operaciones?
- ¿Debe el toolchain soportar localización, IPv6, u otras características especiales?

## Compilando el toolchain

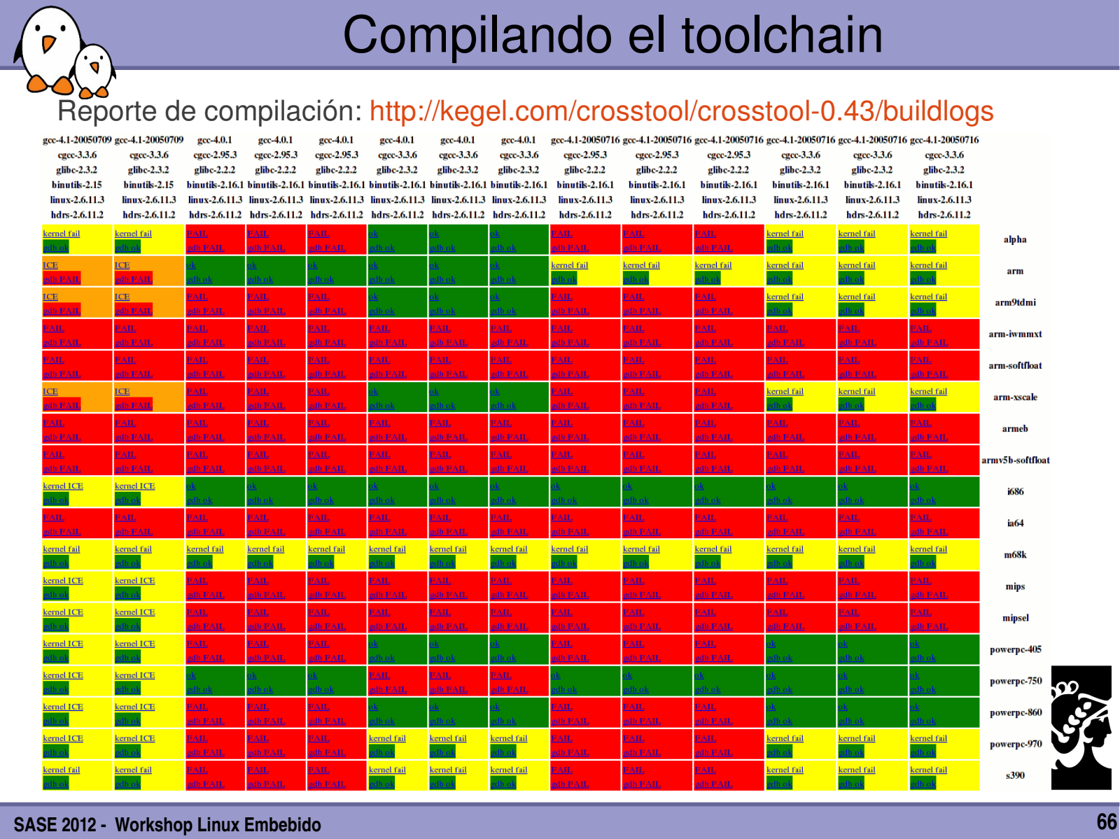
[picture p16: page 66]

SASE 2012 Workshop Linux Embebido | 66

Reporte de compilación: http://kegel.com/crosstool/crosstool-0.43/buildlogs (http://kegel.com/crosstool/crosstool-0.43/buildlogs)

SASE 2012 Workshop Linux Embebido | 67

## Pasos básicos

Extraer e instalar los Kernel headers.
Extraer, configurar, compilar e instalar binutils.
Extraer, configurar y compilar la primera versión del GCC que genera binarios para el target. Lo vamos usar para compilar la librería de C de crosscompilación.
Extraer, configurar y compilar la librería de C con el compilador generado en el paso anterior.
Re configurar y compilar el gcc, contra la nueva librería de
C. Así obtenemos el gcc que vamos a usar.

SASE 2012 Workshop Linux Embebido | 68

## Toolchains caseros

Compilar un cross toolchain a mano es una tarea dolorosa y difícil. Podemos tardar varios días en lograrlo!
Muchos detalles que saber y entender. Muchos componentes que compilar.
Muchas decisiones para tomar.
(configuración de la librería de C para tu plataforma)
Necesitamos fuentes de muchos programas diversos. Estar familiarizado con los problemas actuales del gcc y los parches para tu arquitectura.
Es útil tener práctica compilando programas complejos. http://www.aleph1.co.uk/armlinux/docs/toolchain/toolchHOWTO.pdf ¡Te dice cuán entretenido puede ser!

SASE 2012 Workshop Linux Embebido | 69

## Usar toolchains precompilados

La elección más popular, por ser lo más simple y fácil. Primero, hay que determinar qué toolchain se necesita. CPU, endianism, librería de C, componentes, ABI, punto flotante, etc..
Existen muchos toolchains precompilados:
- CodeSourcery, http://www.codesourcery.com, es una referencia en el área. No te proveen Linux+uClibc.
- Linaro mantiene toolchains optimizados para ARM: https://wiki.linaro.org/WorkingGroups/ToolChain (Linaro contrató a CodeSourcery y agregó cosas)
- Más información en http://elinux.org/Toolchains

SASE 2012 Workshop Linux Embebido | 70

## Usando toolchains precompilados

Seguir las instrucciones provistas por el fabricante. Usualmente es cuestión de descomprimir el archivo y dejarlo en el lugar correspondiente:
- ¡Los toolchains no suelen ser reubicables!
Los tenés que tener en el lugar donde fueron diseñados.
- A partir de gcc 4.x esto no es necesario, pero suele ser lo más común y sencillo.
Finalmente, agregar el toolchain a nuestro PATH:
export PATH=/path/to/toolchain/bin/:$PATH

SASE 2012 Workshop Linux Embebido | 71

## Herramientas para compilar

Otra solución es usar utilidades que automatizan el proceso de creación de un toolchain.
Las mismas ventajas que los precompilados, no hay que meterse con la tediosa compilación manual.
Ofrecen mayor flexibilidad que los toolchains ya compilados. Puedo seleccionar todas las opciones que quiero.
Usualmente incluyen los parches recomendables para los distintos componentes en las distintas arquitecturas.
Son scripts de shell o Makefiles que automatizan el proceso de descargar, extraer, configurar y compilar los distintos componentes.

SASE 2012 Workshop Linux Embebido | 72

Crosstool
- Herramienta original, escrita por Dan Kegel
- Conjunto de scripts y parches, glibconly
- No se mantiene más
- http://www.kegel.com/crosstool
Crosstoolng
- Reescritura de Crosstool, con una sistema de configuración del estilo de menuconfig.
- Más prestaciones: soporta uClibc, glibc, eglibc, hard y soft float, muchas arquitecturas.
- Activamente mantenido.
- http://ymorin.isageek.org/dokuwiki/projects/crosstool (http://ymorin.is-a-geek.org/dokuwiki/projects/crosstool)

## Herramientas para compilar

SASE 2012 Workshop Linux Embebido | 73

## Herramientas para compilar

Muchas herramientas para hacer rootfs también permiten compilar el toolchain.
Buildroot
- Basado en Makefile, sólo uClibc, mantenido por la comunidad. http://buildroot.uclibc.org
PTXdist
- Basado en Makefile, uClibc o glibc, mantenido principalmente por Pengutronix
- http://www.pengutronix.de/software/ptxdist/index_en.html OpenEmbedded
- El sistema de compilación más completo y complejo disponible.
- http://www.openembedded.org/

## Práctica – Usando CrosstoolNG

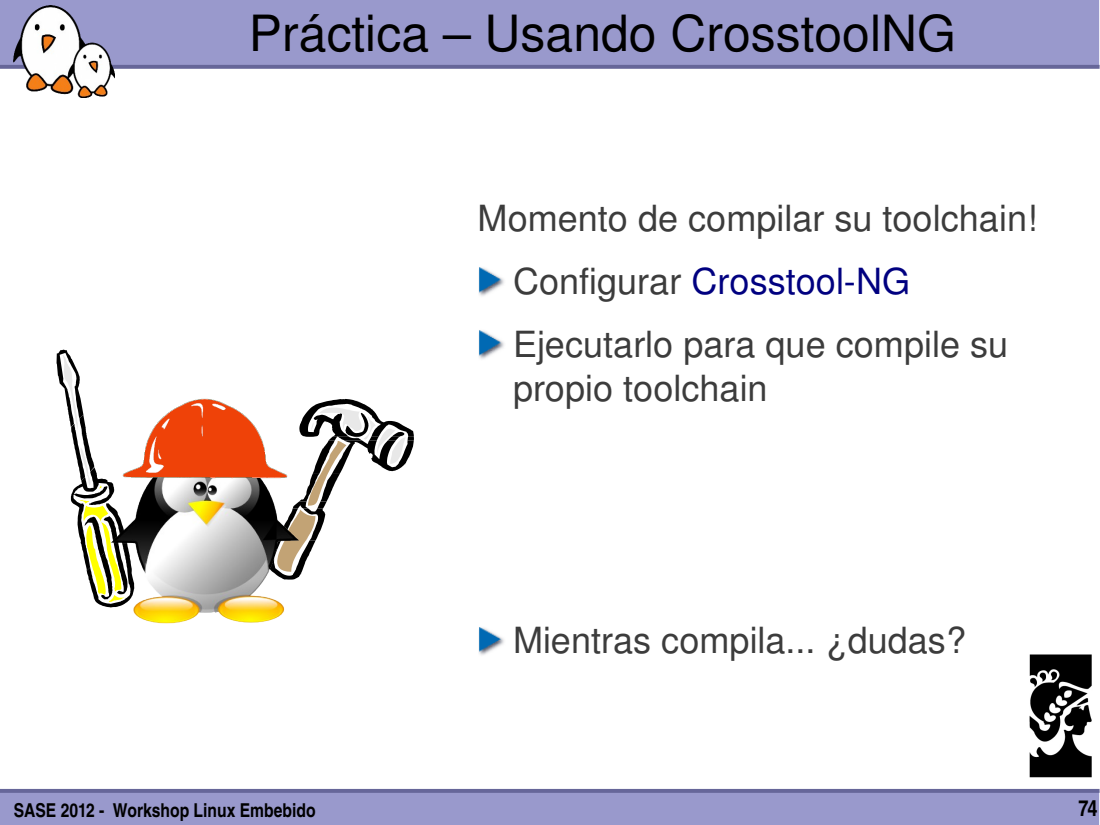
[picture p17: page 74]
SASE 2012 Workshop Linux Embebido

Momento de compilar su toolchain!
Configurar Crosstool-NG
Ejecutarlo para que compile su
propio toolchain

Mientras compila... ¿dudas?

## Linux embebido

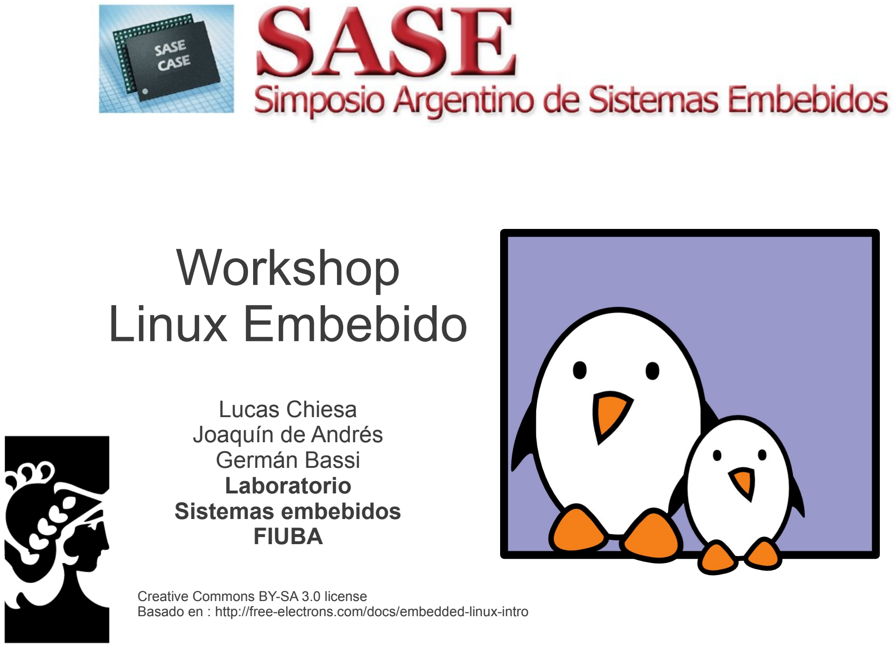
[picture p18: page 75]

## Workshop Linux Embebido

Lucas Chiesa
Joaquín de Andrés
Germán Bassi
Laboratorio
Sistemas embebidos
FIUBA

Creative Commons BY-SA 3.0 license
Basado en : http://free-electrons.com/docs/embedded-linux-intro

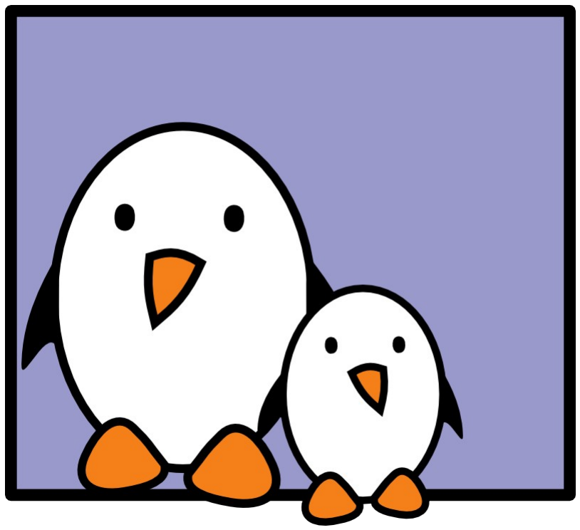
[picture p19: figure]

SASE 2012 Workshop Linux Embebido | 76

## Desarrollo de sistemas Linux

# Bootloaders

SASE 2012 Workshop Linux Embebido | 77

## Bootloaders

El bootloader es un programa responsable de:
- Inicialización básica del hardware.
- Cargar una aplicación binaria, usualmente el Kernel del SO, desde un almacenamiento flash, desde la red, o desde cualquier otro tipo de almacenamiento no volátil.
- Descompresión eventual de la aplicación binaria.
- Ejecución de la aplicación.
Además de las funciones básicas, la mayoría de los bootloaders proveen un shell que implementan diferentes operaciones.
- Inspección de memoria, diagnóstico de hardware, testeo, etc..

SASE 2012 Workshop Linux Embebido | 78

## Bootloaders on x86

Los procesadores x86 son usados típicamente en placas que contienen memoria no volátil donde se encuentra un programa, la BIOS.
El programa es ejecutado desde la CPU después de un reset y es responsable de la inicialización básica del hardware y cargar una pequeña porción de código de almacenamiento no volátil.
- Este código es usualmente los primeros 512 bytes de un disco rígido.
Este código usualmente es la primera etapa del bootloader (1º stage bootloader), que va a cargar el bootloader “real”. Luego, el bootloader puede ofrecer todas sus características. Típicamente entienden sistemas de archivos, para cargar el Kernel directo del FS.

SASE 2012 Workshop Linux Embebido | 79

## Bootloaders on x86

GRUB, Grand Unified Bootloader, es el más poderoso. http://www.gnu.org/software/grub/
- Puede leer muchos sistemas de archivos y cargar el Kernel y su configuración. Provee un shell muy poderoso con muchos comandos. Soporte de red, etc.
LILO, el bootloader original de Linux http://freshmeat.net/projects/lilo/
Syslinux, para bootear de red o de medios http://syslinux.zytor.com

SASE 2012 Workshop Linux Embebido | 80

## Bootloaders en embebidos

En arquitecturas embebidas, el booteo de bajo nivel depende de cada CPU y cada placa.
- Algunas placas tienen una NOR flash de la cual la CPU comienza la ejecución después del reset. En ese caso, el bootloader se debe grabar directamente en la dirección apropiada de esa NOR.
- Algunas CPUs tiene código de booteo integrado en una ROM interna que automáticamente carga una porción de NAND flash en SRAM. En ese caso un bootloader mínimo de primera etapa se debe cargar en ese lugar de NAND. Luego, éste va a cargar el bootloader definitivo en DRAM y ejecutarlo. (BootROM on AT91SAM CPUs, Steppingstone on S3C24xx CPUs, etc.).
El bootloader en embebidos inicia justo después de un reset de la CPU. Debe inicializar todos los dispositivos, incluyendo el controlador de memoria para poder acceder a la DRAM.
Como el proceso de booteo es altamente dependiendo del fabricante es necesario tener la documentación propia del equipo.

SASE 2012 Workshop Linux Embebido | 81

## Bootloaders en embebidos

Nos vamos a centrar en el bootloader principal, por ser el más genérico y por ofrecer la mayor cantidad de prestaciones. Hay varios bootloaders libres genéricos.
Estos son los más populares:
- U-Boot, el “universal bootloader” por Denx
El más usado en ARM, también usado en PPC, MIPS, x86, m68k, NIOS, etc. El estándar defacto actual, y es el que vamos a utilizar. http://www.denx.de/wiki/U-Boot (http://www.denx.de/wiki/U-Boot)
- Barebox, un nuevo bootloader escrito como sucesor a U-Boot. Mejor diseño, mejor código y en desarrollo activo pero todavía no tiene tanto soporte de hardware como U-Boot.
http://www.barebox.org
Hay muchos otros bootloaders, libres y propietarios, usualmente específicos para alguna arquitectura.
- RedBoot, Yaboot, PMON, etc.

SASE 2012 Workshop Linux Embebido | 82

## Desarrollo de sistemas Linux

## Accediendo a una consola serie

SASE 2012 Workshop Linux Embebido | 83

## Minicom

Definición: programa de comunicación serie. Disponible en todas las distribuciones GNU / Linux. Capacidades:
- Consola serie a un sistema Unix remoto
- Transferencia de archivos
- Controlar módems y dialup
- Configuración del puerto serie

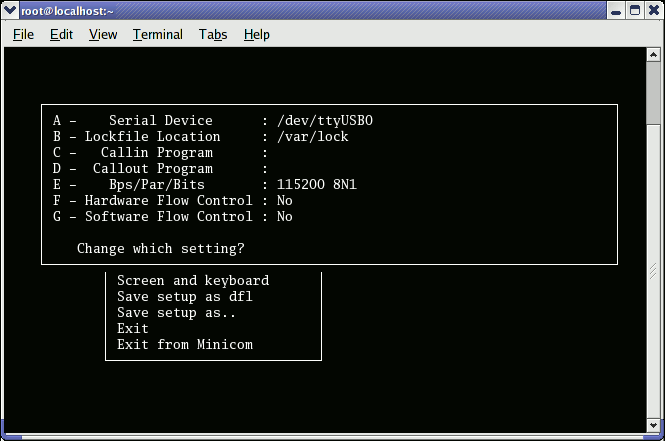
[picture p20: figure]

SASE 2012 Workshop Linux Embebido | 84

## Minicom

Abrirlo ejecutando
minicom s para
configurar minicom
Un poco austero al
principio, pero después
resulta amistoso.

SASE 2012 Workshop Linux Embebido | 85

## Otras terminales series

GTKTerm: http://www.jlsinfo.com/julien/linux/ (http://www.jls-info.com/julien/linux/)
Gráfico. Menos poderoso que Minicom, pero con una interfaz más simple y más atractiva. Disponible en distros recientes. CuteCom: http://cutecom.sourceforge.net/
Otra terminal gráfica amistosa. Disponible en distros recientes. picocom: http://freshmeat.net/projects/picocom/
Emulador muy pequeño (20K), se puede usar embebido
GNU Screen: también se puede usar como terminal serie: screen <device> <baudrate>
Ejemplo:
screen /dev/ttyS0 115200

## Práctica – Bootloaders

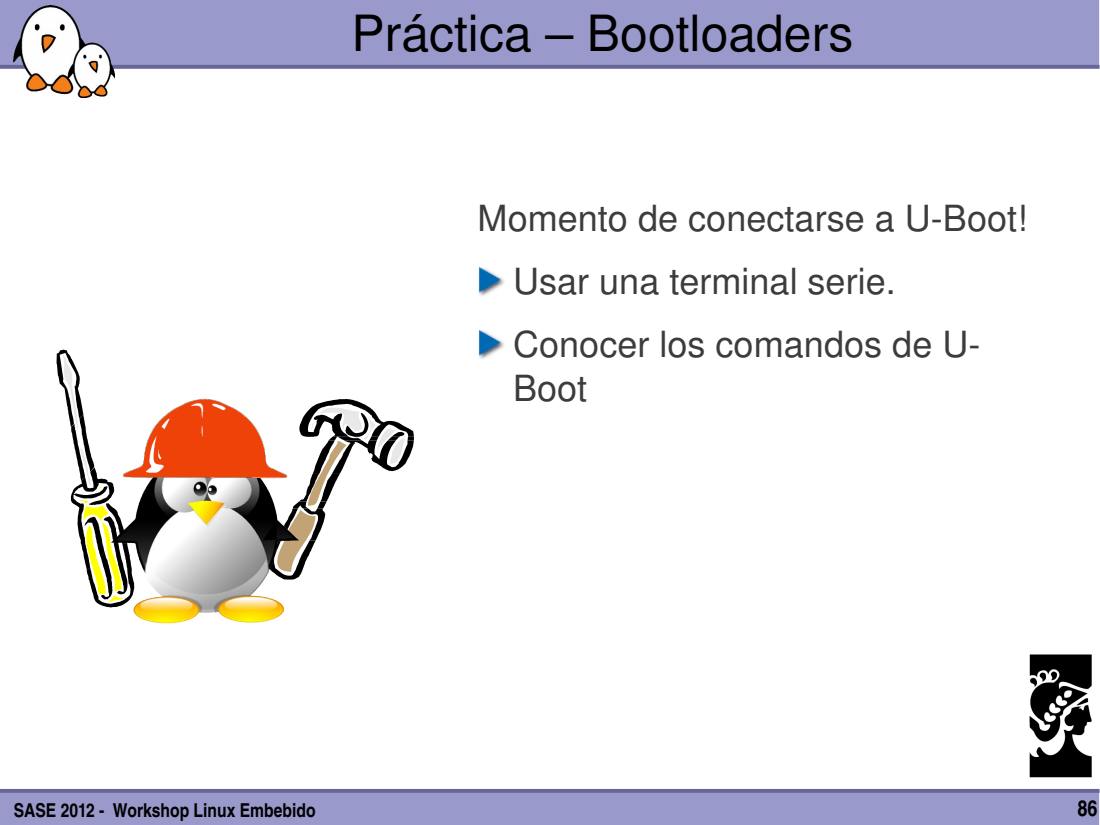
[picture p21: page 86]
SASE 2012 Workshop Linux Embebido

Momento de conectarse a U-Boot!
Usar una terminal serie.
Conocer los comandos de U-
Boot

SASE 2012 Workshop Linux Embebido | 87

## Uso embebido del Kernel Linux

# Uso embebido del Kernel Linux

SASE 2012 Workshop Linux Embebido | 88

## Contenidos

Compilando y booteando
Fuentes del Kernel
Configuración del Kernel
Compilando el Kernel
Inicio del sistema
Archivos de dispositivos
Cross compilando el Kernel

SASE 2012 Workshop Linux Embebido | 89

## Uso embebido del Kernel Linux

## Compilando y Booteando el Kernel

Fuentes del Kernel Linux

SASE 2012 Workshop Linux Embebido | 90

## Fuentes del Kernel

La versión oficial del Kernel, liberada por Linus Torvals, está disponible en http://www.kernel.org
- Esta versión sigue el modelo de desarrollo descripto anteriormente.
- Sin embargo, puede no contener los últimos cambios de un área específica. Algunos cambios pudieron darse después de la ventana de merge o estar todavía en desarrollo.
Muchas subcomunidades del Kernel mantienen sus propias versiones, usualmente con funciones más nuevas y menos estables.
- Comunidades de arquitecturas (ARM, MIPS, PowerPC, etc.), comunidades de drivers (I2C, SPI, USB, PCI, red, etc.), otras comunidades (realtime, etc.)
- Usualmente no liberan versiones oficiales sino que mantienen las ramas de desarrollo.

SASE 2012 Workshop Linux Embebido | 91

## Tamaño del Kernel Linux

Fuentes del Linux 2.6.31:
Tamaño crudo: 350 MB (30,900 archivos, ~ 12,000,000 líneas) gzip: 75 MB
bzip2: 59 MB (mejor)
lzma: 49 MB (el mejor)
Un Linux mínimo 2.6.29 compilado con la opción CONFIG_EMBEDDED, para bootear en un QEMU PC (disco IDE, ext2 filesystem, binarios ELF): 532 KB (comprimido), 1325 KB (descomprimido)
¿Por qué son tan grandes las fuentes?
Proveen miles de drivers, muchos protocolos de red, muchas arquitecturas, muchos sistemas de archivos, etc...
El núcleo de Linux (scheduler, manejador de memoria...) es bastante chico.

SASE 2012 Workshop Linux Embebido | 92

## Tamaño del Kernel Linux

arch
block
crypto
Documentation
drivers
fs
include
init
ipc
kernel
lib
mm
net
scripts
security
sound
usr
0 | 50000 | 100000 | 150000

Tamaño del fuente de Linux por directorios (KB)

Linux 2.6.17
Medido con:
du s apparentsize

SASE 2012 Workshop Linux Embebido | 93

## Bajando las fuentes

Archivos completos
- Contiene las fuentes completas del kernel.
- Bastante para bajar y para descomprimir. Es necesario hacerlo por lo menos una vez.
- Ejemplo: http://kernel.org/pub/linux/kernel/v2.6/linux-2.6.14.7.tar.bz2 Parches incrementales entre versiones
- Asume que tenés una versión base y que aplicaste todos los parches en el orden correcto.
- Rápido para bajar y aplicar
- Ejemplo
http://kernel.org/pub/linux/kernel/v2.6/patch-2.6.14.bz2 (2.6.13 to 2.6.14) http://kernel.org/pub/linux/kernel/v2.6/patch-2.6.14.7.bz2 (2.6.14 to 2.6.14.7)
Todas las versiones anteriores están disponibles en: http://kernel.org/pub/linux/kernel/

SASE 2012 Workshop Linux Embebido | 94

## Aplicando un parche a Linux

Siempre aplicar a la versión x.y.<z-1> Se pueden bajar comprimidos en gzip, bzip2.
Siempre producidos para n=1
Ejemplo:
cd linux-2.6.13
bzcat ../patch-2.6.14.bz2 | patch p1
bzcat ../patch-2.6.14.7.bz2 | patch p1
cd ..; mv linux-2.6.13 linux-2.6.14.7
Mantener el archivo comprimido: Sirve para verificar la firma.
Uno puede ver y editar el archivo sin descomprimirlo usando vim: vim patch-2.6.14.bz2 ((des)compresión on the fly)

Podés hacer patch 30%
más rápido usando sp1
en lugar de p1
(silent)

## Práctica – Fuentes del Kernel

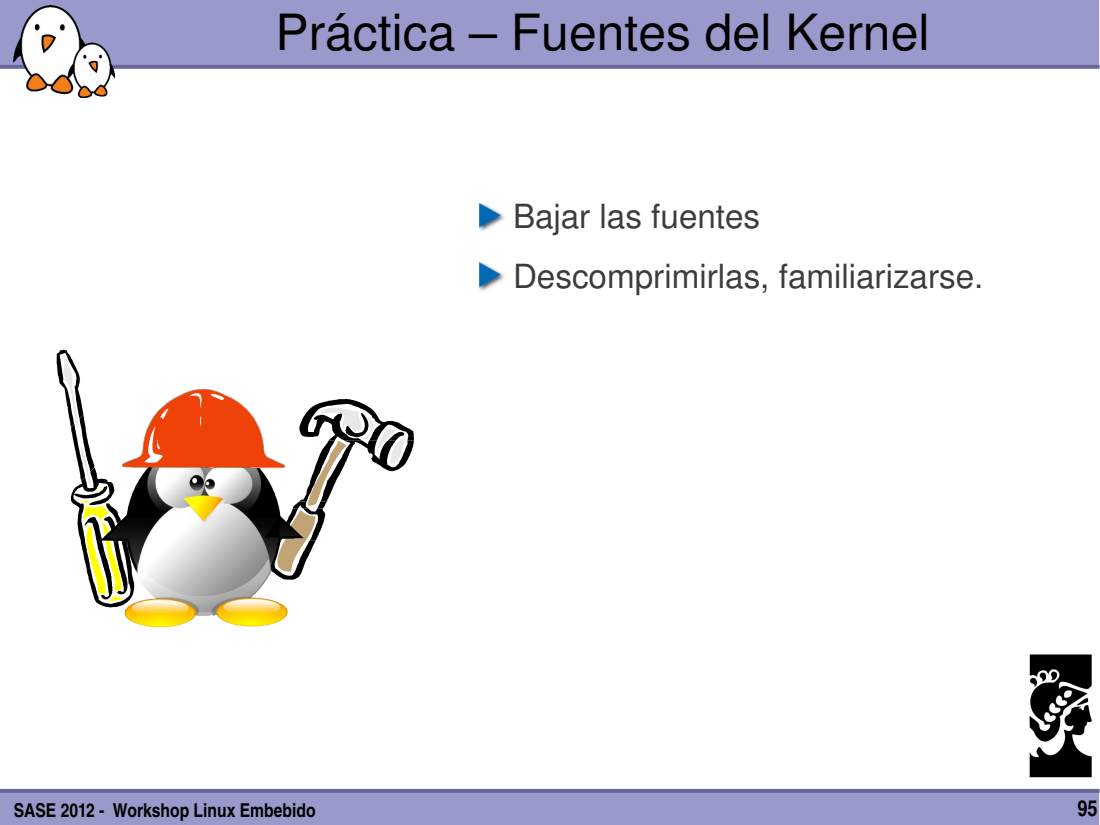
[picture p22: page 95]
SASE 2012 Workshop Linux Embebido

Bajar las fuentes
Descomprimirlas, familiarizarse.

SASE 2012 Workshop Linux Embebido | 96

## Uso embebido del Kernel Linux

## Compilando y booteando

Configuración del Kernel

SASE 2012 Workshop Linux Embebido | 97

## Configuración del Kernel

Ya vimos que el Kernel contiene miles de drivers y otras cosas. Provee miles de opciones para compilar selectivamente diferentes partes del código.
La configuración del Kernel es el proceso de selección de las opciones que queremos que tenga nuestro Kernel
Este conjunto de opciones depende de
- Nuestro hardware
- De las prestaciones que necesitamos del Kernel

SASE 2012 Workshop Linux Embebido | 98

## Configuración del Kernel

La configuración se guarda en el archivo .config en la raíz de las fuentes
- Archivo de texto plano, estilo key=value
Como las opciones tienen dependencias es raro editar el archivo a mano. Se usan interfaces gráficas:
- make [xconfig|gconfig|menuconfig|oldconfig]
- Estos son targets del Makefile del Kernel. Correr make help nos da una lista de targets disponibles.
Para cambiar el Kernel en una distro GNU/Linux:
la configuración usada normalmente está en /boot/, junto con la imagen del Kernel: /boot/config-2.6.17-11-generic

SASE 2012 Workshop Linux Embebido | 99

## make xconfig

make xconfig
La interfaz gráfica más común.
Antes de usar leer:
help > introduction: datos útiles! File browser: facilita cargar archivos de configuración Interfaz de búsqueda de parámetros
Paquetes de Debian / Ubuntu requeridos: libqt3-mtdev, g++

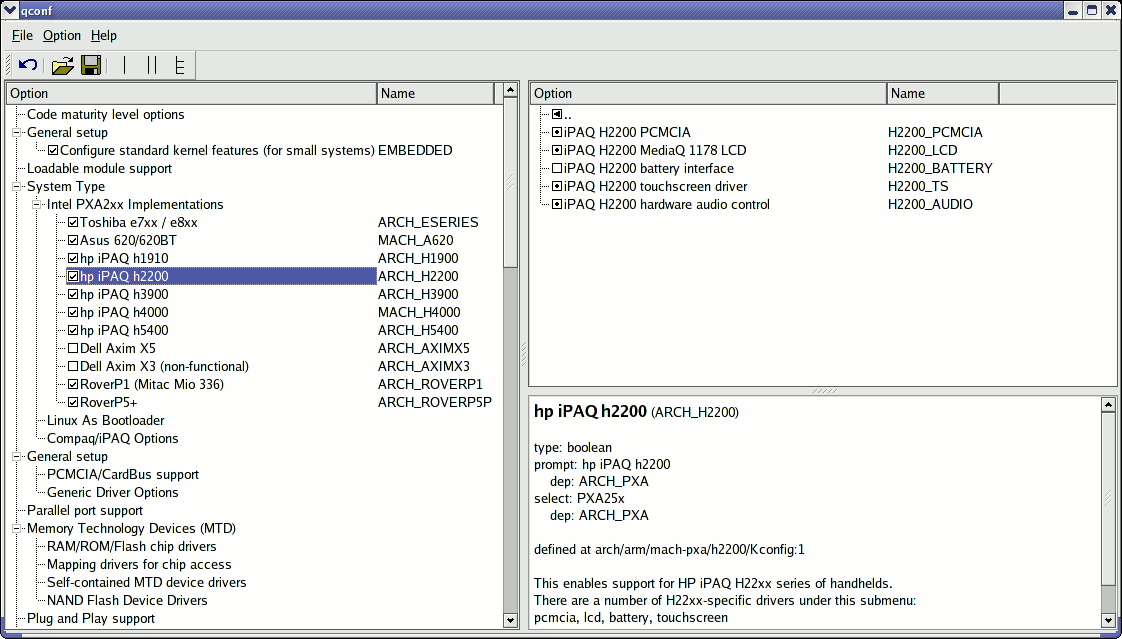
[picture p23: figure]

SASE 2012 Workshop Linux Embebido | 100

## make xconfig screenshot

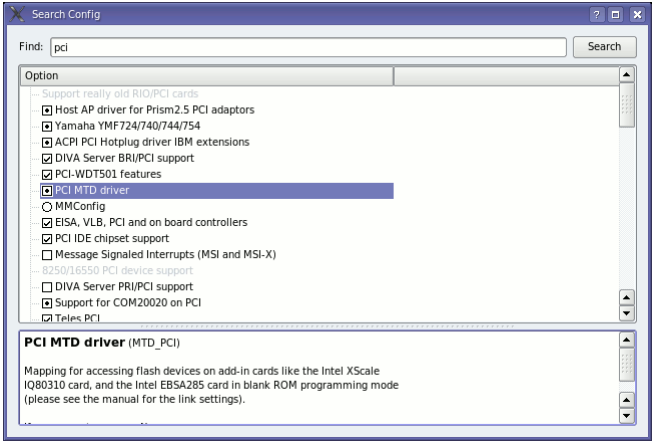
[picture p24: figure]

SASE 2012 Workshop Linux Embebido | 101

## make xconfig: búsqueda

Busca una palabra
cable en las
descripciones
Te deja activar o no
las opciones
encontradas.

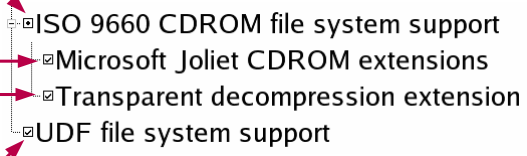
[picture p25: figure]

SASE 2012 Workshop Linux Embebido | 102

## Opciones de configuración

Compilado como módulo (archivo separado) CONFIG_ISO9660_FS=m

Opciones del driver
CONFIG_JOLIET=y
CONFIG_ZISOFS=y

Compilado estático en el Kernel CONFIG_UDF_FS=y

SASE 2012 Workshop Linux Embebido | 103

## .config correspondiente

# CD-ROM/DVD Filesystems

CONFIG_ISO9660_FS=m
CONFIG_JOLIET=y
CONFIG_ZISOFS=y
CONFIG_UDF_FS=y
CONFIG_UDF_NLS=y
# DOS/FAT/NT Filesystems

# CONFIG_MSDOS_FS is not set # CONFIG_VFAT_FS is not set CONFIG_NTFS_FS=m

# CONFIG_NTFS_DEBUG is not set CONFIG_NTFS_RW=y

Nombre de la sección
(ayuda a encontrar settings)

Todos los parámetros comienzan con CONFIG_

SASE 2012 Workshop Linux Embebido | 104

## Dependencias de las opciones

Hay dependencias entre las opciones del Kernel
Por ejemplo, activar un driver de red necesita tener el stack de red compilado.
Dos tipos de dependencias:
- Dependencias “depends on”. En este caso, la opción A que depende de B no es visible hasta que B no esté activada.
- Dependencias “select”. En este caso, si trato de activar la opción A, entonces B es seleccionada automáticamente.
- make xconfig permite ver todas las opciones, incluidas las que no se pueden seleccionar por faltar dependencias. En ese caso, las muestra en color gris.

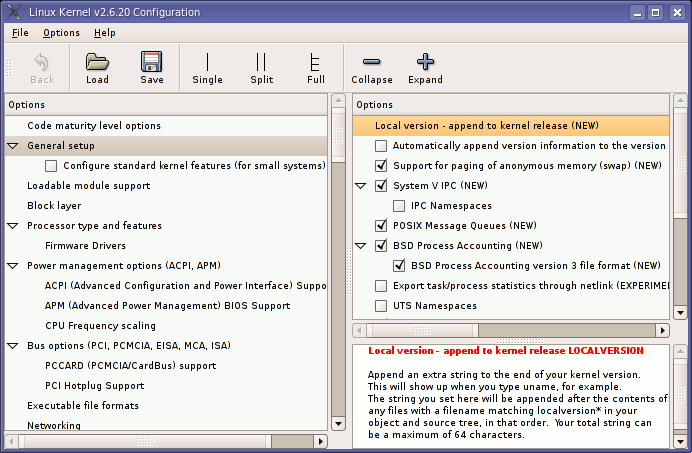
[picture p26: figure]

SASE 2012 Workshop Linux Embebido | 105

## make gconfig

make gconfig
Nuevo frontend basado
en GTK. Funcionalidad
similar a la de make
xconfig.
No se puede buscar.
Paquetes requeridos:
libglade2-dev


SASE 2012 Workshop Linux Embebido | 106

## make menuconfig

make menuconfig
Útil cuando no tengo
interfaz gráfica. Muy
cómoda también!
Misma interfaz que se
usa en otras
herramientas: BusyBox,
buildroot...
Paquetes requeridos:
libncursesdev

SASE 2012 Workshop Linux Embebido | 107

## make oldconfig

make oldconfig
¡Frecuentemente necesario!
Usado para actualizar un archivo .config de una versión anterior del Kernel
Emite advertencias cuando se usaron configuraciones que no existen más en el nuevo Kernel
Pregunta por el valor de nuevas opciones
Si se edita a mano el .config es muy recomendable ejecutar make oldconfig después!

SASE 2012 Workshop Linux Embebido | 108

## make allnoconfig

make allnoconfig
Sólo activa las funciones fuertemente recomendadas Todo lo demás, no lo compila.
Muy útil para partir de lo mínimo y agregar lo que necesitamos.
¡Más fácil agregar lo poco que necesitamos que sacar todo lo que sobra!

SASE 2012 Workshop Linux Embebido | 109

Deshaciendo cambios en la conf.

Un problema frecuente:
Después de varios cambios de configuraciones el Kernel deja de funcionar.
Si uno no se acuerda todos los cambios que fue haciendo, se puede recuperar la configuración anterior: > cp .config.old .config
Todas las interfaces de configuración
(xconfig, menuconfig, allnoconfig...) mantienen una copia de seguridad en .config.old.

SASE 2012 Workshop Linux Embebido | 110

## Configuraciones por arquitectura

El conjunto de configuraciones depende de la arquitectura
- Algunas configuraciones son muy específicas.
- La mayoría de las opciones (opciones globales del Kernel, subsistema de red, filesystems) son visibles en todas las archs. Por omisión, el sistema de compilación asume una compilación nativa.
La arquitectura no se especifica entre las opciones de compilación, sino en un nivel superior.
Vamos a ver cómo seleccionar la arquitectura que queremos.

SASE 2012 Workshop Linux Embebido | 111

## Uso embebido del Kernel Linux

## Compilando e instalando el Kernel Para el sistema host

SASE 2012 Workshop Linux Embebido | 112

## Compilación del kernel

make
- En el directorio principal del código
- Recordar de usar make j n si tenes más de un core n=cores+1
- No tenés que ser root!
Genera
- vmlinux, imagen cruda, sin comprimir en formato ELF, útil para debugging pero no puede ser booteado.
- arch/<arch>/boot/*Image, la imagen final, usualmente comprimida y puede ser booteada.
– bzImage para x86, zImage para ARM, vmImage.gz para Blackfin, etc.
- Los módulos de kernel están distribuidos por todas las fuentes y son archivos que terminan en .ko.

SASE 2012 Workshop Linux Embebido | 113

## Instalación del Kernel

make install
- Instala el Kernel en el sistema host. Se debe correr como root. Instala
- /boot/vmlinuz<version>
La imagen del Kernel comprimida. La misma que en arch/<arch>/boot
- /boot/System.map<version>
Guarda la dirección de los símbolos del Kernel
- /boot/config<version>
Configuración del Kernel para esa versión
- Usualmente ejecuta la utilidad de configuración del bootloader para incorporar el nuevo Kernel

SASE 2012 Workshop Linux Embebido | 114

## Instalación de los módulos

make modules_install
- Instala los módulos en el sistema host. Se debe ejecutar como root. Instala los módulos en /lib/modules/<version>/
- kernel/
Guarda todos archivos los .ko (Kernel Object), manteniendo la estructura de las fuentes.
- modules.alias
Archivo usado por las herramientas que cargan módulos. Por ejemplo:
alias soundservice?-0 snd_mixer_oss
- modules.dep
Dependencias de los módulos
- modules.symbols
Muestra a qué módulo corresponde cada símbolo.


SASE 2012 Workshop Linux Embebido | 115

## Limpiando la fuentes

Limpiar los archivos generados por compilación (para forzar a compilar todo nuevamente):
make clean
Borra todos los archivos generados. Usado cuando cambiamos de arquitectura
Cuidado: también borra el archivos .config! make mrproper
También borrar los archivos de backup y archivos generados por patch. Útil cuando se está haciendo un parche.
make distclean

SASE 2012 Workshop Linux Embebido | 116

## Uso embebido del Kernel Linux

## Compilando y booteando Linux

Archivos de dispositivos

SASE 2012 Workshop Linux Embebido | 117

## Dispositivos de caracteres

Se acceden como un flujo secuencial de caracteres individuales
Se identifican por el tipo c
(ls l):
crwrw 1 root uucp | 4, 64 Feb 23 2004 /dev/ttyS0
crww 1 jdoe tty 136, | 1 Feb 23 2004 /dev/pts/1
crw 1 root root 13, 32 Feb 23 2004 /dev/input/mouse0
crwrwrw 1 root root | 1, | 3 Feb 23 2004 /dev/null
Ejemplos: teclados, mouse, puerto paralelo, IrDA, Bluetooth port, consolas, terminales, etc...

SASE 2012 Workshop Linux Embebido | 118

## Dispositivos de bloques

Se acceden por bloques de datos de algún tamaño fijo. Pueden ser leídos en cualquier orden.
Se identifican por el tipo de archivo b (ls l):
brwrw | 1 root disk | 3, | 1 Feb 23 2004 hda1
brwrw | 1 jdoe floppy | 2, | 0 Feb 23 2004 fd0
brwrw | 1 root disk | 7, | 0 Feb 23 2004 loop0
brwrw | 1 root disk | 1, | 1 Feb 23 2004 ram1
brw | 1 root root | 8, | 1 Feb 23 2004 sda1
Ejemplos: discos rígidos y floppy, discos ram, dispositivos loop...

SASE 2012 Workshop Linux Embebido | 119

## Números minor y major

Como se ve en los ejemplos anteriores los archivos tienen dos números asociados:
El primero: el número major
El segundo: el número minor
Los números major y minor son números usados por el Kernel para vincular un driver con un dispositivo. Los nombres de los archivos no le importan al Kernel! Para saber a qué driver corresponde cada número, ver Documentation/devices.txt. (http://free-electrons.com/kerneldoc/latest/devices.txt)

SASE 2012 Workshop Linux Embebido | 120

## Creación de los archivos

No se crean cuando se carga el driver
Deben ser creados de antemano:
sudo mknod /dev/<device> [c|b] <major> <minor> Ejemplos:
sudo mknod /dev/ttyS0 c 4 64
sudo mknod /dev/hda1 b 3 1

## Práctica – Configurar y compilar

SASE 2012 Workshop Linux Embebido

Configurar su Kernel
Compilarlo
Bootearlo en una máquina virtual

SASE 2012 Workshop Linux Embebido | 122

## Uso embebido del Kernel Linux

## Compilando y booteando Linux

Inicio general del sistema

SASE 2012 Workshop Linux Embebido | 123

## Secuencia de booteo tradicional

Bootloader
Ejecutado por el hardware desde una posición fija de ROM / Flash Inicializa el soporte de los dispositivos donde se encuentra el kernel. (almacenamiento, red, medios removibles)
Carga el Kernel en RAM
Ejecuta la imagen del Kernel (con unos parámetros determinados)
Kernel
Se auto descomprime
Inicializa el núcleo del Kernel y drivers compilados estáticos (necesarios para acceder al root filesystem)
Monta el root filesystem (especificado por el parámetro root)
Ejecuta el primer programa de userspace (especificado por el parámetro init)
Primer programa de userspace
Configura userspace y continúa levantando servicios

SASE 2012 Workshop Linux Embebido | 124

## Parámetros del Kernel

El Kernel acepta parámetros al momento de bootear
Son parte de la configuración del bootloader
Son copiados a RAM por el bootloader a la posición de RAM donde los espera el Kernel.
Útiles para modificar el comportamiento del Kernel al momento de booteo, sin recompilarlo.
Útiles para hacer inicialización avanzada de drivers y el Kernel sin la necesidad de tener complejos scripts de userspace.

SASE 2012 Workshop Linux Embebido | 125

## Ejemplo de los parámetros

HP iPAQ h2200 PDA ejemplo:
root=/dev/ram0 \ | Root fs (primer ramdisk)
rw \ | Modo de montaje del root fs
init=/linuxrc \ | Primer programa userspace
console=ttyS0,115200n8 \ | Consola (serie)
console=tty0 \ | Otra consola (framebuffer)
ramdisk_size=8192 \ | Otros parámetros...
cachepolicy=writethrough
Cientos de parámetros descriptos en: Documentation/kernelparameters.txt (http://free-electrons.com/kerneldoc/latest/kernel-parameters.txt)

SASE 2012 Workshop Linux Embebido | 126

## Desventajas

Se asume que todos los drivers necesarios para montar el root fs (almacenamiento y fs) están compilados estáticos en el kernel. Se puede asumir en la mayoría de los sistemas embebidos que esto va a pasar, donde el hardware es conocido y el kernel está afinado al sistema.
Es usualmente errónea en los sistemas desktop y servers donde una imagen tiene que levantar en una cantidad de dispositivos muy grande.
- Se necesita más flexibilidad
- Los módulos te dan esta flexibilidad, pero no están disponibles hasta montar el root filesystem.
- Necesidad de soportar sistemas complejos (RAID, NFS, etc.)

SASE 2012 Workshop Linux Embebido | 127

## Solución

Una solución es incluir un pequeño rootfs temporal con los módulos necesarios dentro del Kernel mismo. Este sistema de archivos se llama initramfs.
El initramfs es un sistema de archivos comprimido cpio con un rootfs muy básico.
- Un cpio es como un zip pero con un formato mucho más simple. Los scripts del initramfs van a detectar el hardware, cargar los módulos necesarios y montar el rootfs real.
Finalmente, el los scripts del initramfs van a correr la aplicación init del rootfs real y continuar el booteo usual.
Esta técnica reemplaza completamente los init ramdisks (initrds), que se usaban con Linux 2.4, pero no son más necesarios.

SASE 2012 Workshop Linux Embebido | 128

## Secuencia de booteo con initramfs

Bootloader
Ejecutado por el hardware desde una posición fija de ROM / Flash
Inicializa el soporte de los dispositivos donde se encuentra el kernel. (almacenamiento, red, medios removibles)
Carga el Kernel en RAM
Ejecuta la imagen del kernel (con unos parámetros determinados

Kernel
Se descomprime
Inicializa el núcleo y los drivers compilados estáticos.
Descomprime el archivo cpio del initramfs. (si existe, dentro del kernel, sino el bootloader lo copia a una parte específica de memoria) y lo extrae en el cache del kernel.
Si encontró un initramfs, ejecuta el primer programa dentro del initramfs. /init

Userspace: script /init (es lo mismo que un userspace normal)
Corre comandos para configurar el dispositivo
(configuración de red, montar /proc y /sys...)
Monta el rootfs. Cambiar a ese filesystem (switch_root)
Corre /sbin/init

Userspace: /sbin/init
Configura lo que no esté configurado por el initramfs.
Levanta los servicios (demonios, servers) y programas de usuario

Sin

c

a

m

bio

s

SASE 2012 Workshop Linux Embebido | 129

## Ventajas initramfs

Es una solución simple, meter un rootfs directo en el kernel o copiado por el bootloader.
Es simplemente un archivo cpio comprimido que se extrae al cache de archivos. No necesita un bloque ni un driver de filesystem.
Es más montar filesystem complejos desde scripts de userspace que desde código de kernel. Mueve la complejidad a espacio de usuario.
Posibilita agregar archivos no GPL (firmware, drivers propietarios) en el filesystem. Esto no es linking, por lo que no es una violación de la GPL.

SASE 2012 Workshop Linux Embebido | 130

## Como poblar un initramfs

Usando CONFIG_INITRAMFS_SOURCE
en la configuración del Kernel (General Setup) Se le puede dar un cpio existente
O darle un directorio para ser archivado.

ver Documentation/filesystems/ramfsrootfsinitramfs.txt
y Documentation/earlyuserspace/README en las fuentes del Kernel. También, es http://www.linuxdevices.com/articles/AT4017834659.html hay una linda descripción de initramfs (por Rob Landley).
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

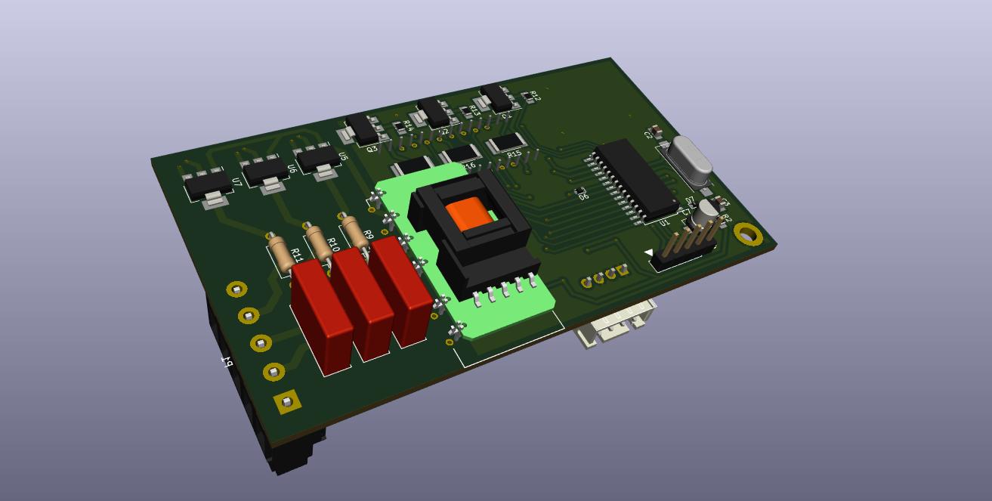
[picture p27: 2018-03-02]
Hartware_2.0.0/doc/D21_2550.jpg

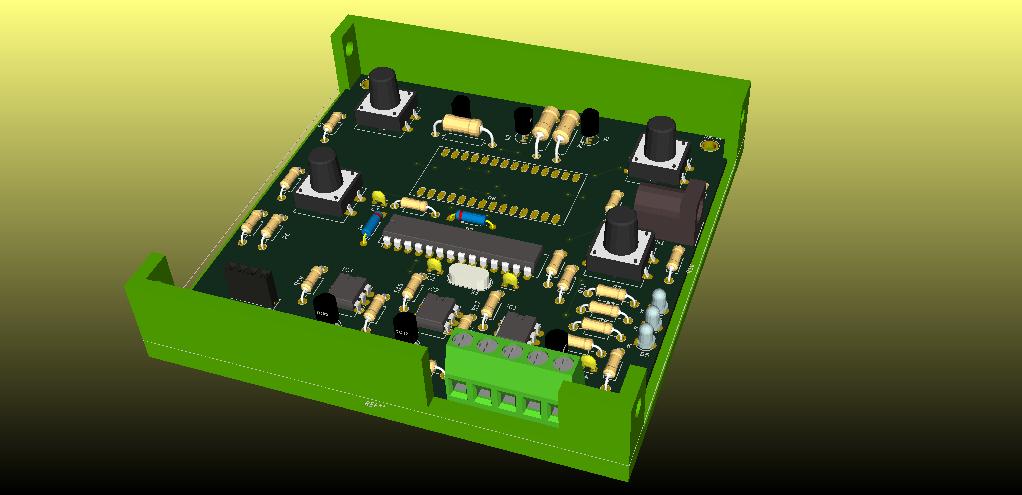
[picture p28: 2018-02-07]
Hartware_1.0.0/CCF.jpg

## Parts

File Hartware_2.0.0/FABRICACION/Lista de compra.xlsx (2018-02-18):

Manufacturer Part Number | Manufacturer | Quantity | Unit Price | Sub | Description
A759KS475M2EAAE496 | KEMET | 2 | $1.44 | $2.88 | CAP ALUM POLY 4.7UF 20% 250V T/H
C0805C103K5RACTU | KEMET | 2 | $0.10 | $0.20 | CAP CER 10000PF 50V X7R 0805
GRM31CR72E104KW03L | Murata Electronics North America | 4 | $0.34 | $1.36 | CAP CER 0.1UF 250V X7R 1206
EEE-1CA100SR | Panasonic Electronic Components | 1 | $0.28 | $0.28 | CAP ALUM 10UF 20% 16V SMD
C2012C0G2W102J060AA | TDK Corporation | 1 | $0.32 | $0.32 | CAP CER 1000PF 450V C0G 0805
EEE-FKC271XSP | Panasonic Electronic Components | 1 | $0.74 | $0.74 | CAP ALUM 270UF 20% 16V SMD
UUD1V680MCL1GS | Nichicon | 1 | $0.52 | $0.52 | CAP ALUM 68UF 20% 35V SMD
1N4148X-TP | Micro Commercial Co | 2 | $0.14 | $0.28 | DIODE GEN PURP 75V 150MA SOD523
150060BS75000 | Wurth Electronics Inc. | 3 | $0.15 | $0.45 | LED BLUE CLEAR 0603 SMD
LTC-4724JR | Lite-On Inc. | 1 | $3.23 | $3.23 | LED 7-SEG .4" 3DGT SUPER RED CC
SDR0503-472JL | Bourns Inc. | 1 | $0.58 | $0.58 | FIXED IND 4.7MH 40MA 48 OHM SMD
74479776247 | Wurth Electronics Inc. | 1 | $0.81 | $0.81 | FIXED IND 4.7UH 1A 160 MOHM SMD
282836-5 | TE Connectivity AMP Connectors | 1 | $1.69 | $1.69 | TERM BLOCK 5POS SIDE ENTRY 5MM
FZT493TA | Diodes Incorporated | 3 | $0.72 | $2.16 | TRANS NPN 100V 1A SOT-223
ERA-6AEB103V | Panasonic Electronic Components | 5 | $0.36 | $1.80 | RES SMD 10K OHM 0.1% 1/8W 0805
ESR10EZPJ331 | Rohm Semiconductor | 6 | $0.10 | $0.60 | RES SMD 330 OHM 5% 0.4W 0805
ERA-6AEB101V | Panasonic Electronic Components | 3 | $0.36 | $1.08 | RES SMD 100 OHM 0.1% 1/8W 0805
ERA-6AEB272V | Panasonic Electronic Components | 3 | $0.36 | $1.08 | RES SMD 2.7K OHM 0.1% 1/8W 0805
RC2512JK-0722RL | Yageo | 3 | $0.22 | $0.66 | RES SMD 22 OHM 5% 1W 2512
RG2012P-203-B-T5 | Susumu | 2 | $0.41 | $0.82 | RES SMD 20K OHM 0.1% 1/8W 0805
ESR10EZPJ221 | Rohm Semiconductor | 3 | $0.10 | $0.30 | RES SMD 220 OHM 5% 0.4W 0805
B72214S0351K101 | EPCOS (TDK) | 1 | $0.52 | $0.52 | VARISTOR DISC 14MM
TL3301AF160QG | E-Switch | 4 | $0.37 | $1.48 | SWITCH TACTILE SPST-NO 0.05A 12V
PIC18F2550-I/SO | Microchip Technology | 1 | $4.38 | $4.38 | IC MCU 8BIT 32KB FLASH 28SOIC
MOC3063S-TA1 | Lite-On Inc. | 3 | $0.72 | $2.16 | OPTOISOLATOR 5KV TRIAC 6SMD
Z0103MN 5AA4 | STMicroelectronics | 3 | $0.87 | $2.61 | TRIAC SENS GATE 600V 1A SOT223
PBO-3-S5 | CUI Inc. | 1 | $7.27 | $7.27 | AC DC CONVERTER 5V 3W
ABLS-20.000MHZ-B2-T | Abracon LLC | 1 | $0.28 | $0.28 | CRYSTAL 20.0000MHZ 18PF SMD
 |  |  | Total | $40.54

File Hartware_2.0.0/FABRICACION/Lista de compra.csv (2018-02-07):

Id | Identificador | Empaquetado | Cantidad | Identificacion | Precio unit | total | Suministrador y ref
1 | R20,R2,R21,R22,R23 | R_0805_HandSoldering | 5 | 10k | 8 | 40 | http://tepuyelectronics.com/resistencias/23-resistencias-smd.html#/valores_de_resistencias-10k
2 | SW4,SW1,SW2,SW3 | SW_PUSH-12mm | 4 | SW_PUSH |  | 0
3 | C4,C5,C6 | C_Disc_D6_P5 | 3 | 100nf | 166,65 | 499,95 | http://electronica.com.ve/new/catalog/product_info.php?cPath=66&products_id=454
4 | D1,D2,D3,D4 | Diode_DO-41_SOD81_Horizontal_RM10 | 4 | 1N4007 | 35,87 | 143,48 | http://electronica.com.ve/new/catalog/product_info.php?products_id=242
5 | D5 | Diode_DO-35_SOD27_Horizontal_RM10 | 1 | 1N4733A | 114,64 | 114,64 | http://electronica.com.ve/new/catalog/product_info.php?cPath=39&products_id=2026
6 | P1 | TerminalBlock_Pheonix_MKDS1.5-5pol | 1 | CONN_01X05 |  | 0
7 | P2,P3 | Pin_Header_Straight_1x02 | 2 | CONN_01X02 |  | 0
8 | U5,U6,U7 | TO-92_Inline_Narrow_Oval | 3 | MAC97A6 | 233,62 | 700,86 | http://electronica.com.ve/new/catalog/advanced_search_result.php?search_in_description=1&x=7&y=3
9 | U8 | 7seg-HDC-19x37.5mm | 1 | HDC-5633 |  | 0
10 | Y1 | Crystal_HC49-U_Vertical | 1 | 4MHZ |  | 0
11 | R3,R4,R5 | R_0805_HandSoldering | 3 | 330 | 8 | 24 | http://tepuyelectronics.com/resistencias/23-resistencias-smd.html#/valores_de_resistencias-470
12 | R12,R13,R14 | R_0805_HandSoldering | 3 | 2.7k | 8 | 24 | http://tepuyelectronics.com/resistencias/23-resistencias-smd.html#/valores_de_resistencias-470
13 | R18,R19 | R_0805_HandSoldering | 2 | 20k | 8 | 16 | http://tepuyelectronics.com/resistencias/23-resistencias-smd.html#/valores_de_resistencias-470
14 | Q1,Q2,Q3 | SOT-23_Handsoldering | 3 | 2N3904 | 40 | 120 | http://tepuyelectronics.com/transistores/36-mmbt3904.html
15 | U2,U3,U4 | DIP-6_W7.62mm_LongPads | 3 | MOC3021M | 576,46 | 1729,38 | http://electronica.com.ve/new/catalog/product_info.php?products_id=652
16 | C2,C3 | C_0805_HandSoldering | 2 | 33pf | 30 | 60 | http://tepuyelectronics.com/capacitores/25-capacitor-ceramico-01uf-50v.html
17 | U1 | SOIC-28_7.5x17.9mm_Pitch1.27mm | 1 | PIC18F2550 | 5578,65 | 5578,65 | http://electronica.com.ve/new/catalog/product_info.php?products_id=199
18 | C7 | C_Radial_D5_L11_P2 | 1 | 10uf |  | 0
19 | D6,D7 | SOD-123 | 2 | 1N4007 | 61 | 122 | http://tepuyelectronics.com/diodos-rectificadores/34-1n4148w.html
20 | D8 | LED-3MM | 1 | D_C | 80 | 80 | http://electronica.com.ve/new/catalog/product_info.php?cPath=25&products_id=3071
21 | D9 | LED-3MM | 1 | D_V | 80 | 80 | http://electronica.com.ve/new/catalog/product_info.php?cPath=25&products_id=3071
22 | D10 | LED-3MM | 1 | D_R | 80 | 80 | http://electronica.com.ve/new/catalog/product_info.php?cPath=25&products_id=3071
23 | P4 | Pin_Header_Straight_1x05 | 1 | CONN_01X05 |  | 0
24 | R15,R16,R17 | Resistor_Horizontal_RM10mm | 3 | 22 | 26,57 | 79,71 | http://electronica.com.ve/new/catalog/product_info.php?cPath=40&products_id=585
25 | R24,R25,R26 | R_0805_HandSoldering | 3 | 220 | 8 | 24 | http://tepuyelectronics.com/resistencias/23-resistencias-smd.html#/valores_de_resistencias-470
26 | R6,R7,R8 | Resistor_Horizontal_RM10mm | 3 | 330 | 26,57 | 79,71 | http://electronica.com.ve/new/catalog/product_info.php?cPath=40&products_id=585
27 | R9,R10,R11 | Resistor_Horizontal_RM10mm | 3 | 100 | 26,57 | 79,71 | http://electronica.com.ve/new/catalog/product_info.php?cPath=40&products_id=585
28 | C1 | C_Radial_D8_L11.5_P3.5 | 1 | 680uf | 414 | 414 | http://electronica.com.ve/new/catalog/product_info.php?cPath=66&products_id=755
29 | C8 | Choke_Horizontal_RM25mm | 1 | 4.7uf | 1000 | 1000 | http://electronica.com.ve/new/catalog/product_info.php?cPath=66&products_id=3067
30 | R1 | Resistor_Horizontal_RM10mm | 1 | 300k | 26,57 | 26,57 | http://electronica.com.ve/new/catalog/product_info.php?cPath=40&products_id=585
31 | R27 | R_0805_HandSoldering | 1 | 100 | 8 | 8 | http://tepuyelectronics.com/resistencias/23-resistencias-smd.html#/valores_de_resistencias-470
 |  |  |  |  | Sub total + IVA | 11124,66
 |  |  |  |  | costo envio | 1400
 |  |  |  |  | mano de obra | 10000
 |  |  |  |  | miselaneos | 5000
 |  |  |  |  | TOTAL | 27.524,66

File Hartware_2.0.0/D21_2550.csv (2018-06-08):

Item | Reference(s) | Description | Qty | Manufacturer | Mfg Part # | Package | Type | Value
1 | C1, C11 |  | 2 |  | A759KS475M2EAAE496 | CP_Radial_D8.0mm_P3.50mm |  | 4,7uF
2 | C2, C3 |  | 2 |  | C0805C103K5RACTU | C_0805_2012Metric_Pad1.15x1.50mm_HandSolder |  | 33pf
3 | C4, C5, C6 |  | 3 |  | R60QF1100AA01K | C_Rect_L13.0mm_W4.0mm_P10.00mm_FKS3_FKP3_MKS4 |  | 1nF
4 | C8 |  | 1 |  | C2012C0G2W102J060AA | C_0805_2012Metric_Pad1.15x1.50mm_HandSolder |  | 1nF
5 | C9 |  | 1 |  | EEE-FKC271XSP | CP_Elec_6.3x7.7 |  | 270uF
6 | C10 |  | 1 |  | UUD1V680MCL1GS | CP_Elec_6.3x7.7 |  | 68uF
7 | C12 |  | 1 |  | C1206C104K5RAC7867 | C_1206_3216Metric_Pad1.24x1.80mm_HandSolder |  | 100nF
8 | D8, D9, D10 |  | 3 |  | 150060BS75000 | LED_0603_1608Metric_Pad0.67x1.00mm_HandSolder |  | LED
9 | D11 |  | 1 |  | LTC-4724JR | LTC-4724JR |  | LTC-4724JR
10 | J1 |  | 1 |  | S4B-XH-A(LF)(SN) | JST_XH_S04B-XH-A-1_1x04_P2.50mm_Horizontal |  | THR
11 |  |  | 1
12 | L1 |  | 1 |  | SDR0503-472JL | SDR0503-XXX |  | SDR0503-472JL
13 | L2 |  | 1 |  | 74479776247 | L_0805_2012Metric_Pad1.15x1.50mm_HandSolder |  | 74479776247
14 | P1 |  | 1 |  | 282836-5 | TerminalBlock_bornier-5_P5.08mm |  | POWER I/O
15 |  |  | 1
16 | Q1, Q2, Q3 |  | 3 |  | FZT493TA | SOT-223 |  | FZT493TA
17 | R1 |  | 1 |  |  | R_1206_3216Metric_Pad1.24x1.80mm_HandSolder |  | 300k
18 | R2, R20, R21, R22, R23 |  | 5 |  | ERA-6AEB103V | R_0805_2012Metric_Pad1.15x1.50mm_HandSolder |  | 10k
19 | R3, R4, R5, R6, R7, R8 |  | 6 |  | ESR10EZPJ331 | R_0805_2012Metric_Pad1.15x1.50mm_HandSolder |  | 330
20 | R9, R10 |  | 2 |  | PR01000103309JR500 | R_Axial_DIN0207_L6.3mm_D2.5mm_P10.16mm_Horizontal |  | 33
21 | R11 |  | 1 |  | PR01000103309JR500 | R_Axial_DIN0207_L6.3mm_D2.5mm_P10.16mm_Horizontal |  | 100
22 | R12, R13, R14 |  | 3 |  | ERA-6AEB272V | R_0805_2012Metric_Pad1.15x1.50mm_HandSolder |  | 2.7k
23 | R15, R16, R17 |  | 3 |  | RC2512JK-0722RL | R_2512_6332Metric_Pad1.34x3.40mm_HandSolder |  | 22
24 | R18, R19 |  | 2 |  | RG2012P-203-B-T5 | R_0805_2012Metric_Pad1.15x1.50mm_HandSolder |  | 20k
25 | R24, R25, R26 |  | 3 |  | ESR10EZPJ221 | R_0805_2012Metric_Pad1.15x1.50mm_HandSolder |  | 220
26 | RV1 |  | 1 |  | B72214S0351K101 | C_Disc_D4.3mm_W1.9mm_P5.00mm |  | B72214S0351K101
27 | SW1, SW2, SW3, SW4 |  | 4 |  | TL3301AF160QG | TL3301AF160QG |  | TL3301AF160QG
28 | U1 |  | 1 |  | PIC18F2550-I/SO | SOIC-28W_7.5x17.9mm_P1.27mm |  | PIC18F2550-ISO
29 | U2, U3, U4 |  | 3 |  | MOC3063S-TA1 | MOC306X |  | MOC3063S-TA1
30 | U5, U6, U7 |  | 3 |  | Z0103MN 5AA4 | SOT-223-Z01 |  | Z0103MN 5AA4
31 | U8 |  | 1 |  | PBO-3-S5 | PBO-3-S5 |  | PBO-3-S5
32 | Y1 |  | 1 |  | ABLS-20.000MHZ-B2-T | Crystal_SMD_ABLS_HC49-SD |  | 20MHZ

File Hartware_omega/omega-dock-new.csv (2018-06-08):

Item | Reference(s) | Description | Qty | Manufacturer | Mfg Part # | Package | Type | Value
1 | BT1 |  | 1 |  | 3000TR | BatteryHolder_Keystone_3000_1x12mm |  | 3V
2 | C1 |  | 1 |  | EEE-HA1V220WR | CP_Elec_5x5.3 |  | 22uF
3 | C5, C6 |  | 2 |  | A759KS475M2EAAE496 | CP_Radial_D8.0mm_P3.50mm |  | 4,7uF
4 | C7 |  | 1 |  | EEE-1VA100SR | CP_Elec_4x5.3 |  | 10uF
5 | C8 |  | 1 |  | C2012C0G2W102J060AA | C_0805_2012Metric_Pad1.15x1.50mm_HandSolder |  | 1nF
6 | C9 |  | 1 |  | EEE-1AA101WR | CP_Elec_4x5.3 |  | 100uF
7 | C10 |  | 1 |  | EEE-FK0J271SP | CP_Elec_6.3x7.7 |  | 270uF
8 | C11 |  | 1 |  | UUD1V680MCL1GS | CP_Elec_6.3x7.7 |  | 68uF
9 | C12 |  | 1 |  | GCM21BR72A104KA37L | C_1206_3216Metric_Pad1.24x1.80mm_HandSolder |  | 100nF
10 | C13, C14, C15 |  | 3 |  | R60QF1100AA01K | C_Rect_L13.0mm_W4.0mm_P10.00mm_FKS3_FKP3_MKS4 |  | 1nF
11 | D1, D2, D3, D4, D7 |  | 5 |  | VLMB1300-GS08 | LED_0603_1608Metric_Castellated |  | LED
12 | D5 |  | 1 |  | MB4S-TP | MBS -1 |  | Bridge
13 | D6 |  | 1 |  | LS Q976-NR-1 | LED_0603_1608Metric_Castellated |  | LED
14 | F1 |  | 2 |  | FC-211-22 | FC-211-22_M |  | 1A
15 | J1 |  | 1 |  | DF1BZ-3P-2.5DS | HE_XDF1B_1x03_P2.50mm_Horizontal |  | SI
16 | J2 |  | 1 |  | DF1BZ-4P-2.5DS | JST_XH_S04B-XH-A-1_1x04_P2.50mm_Horizontal |  | Termistor
17 | L2 |  | 1 |  | SDR0503-472JL | SDR0503-XXX |  | SDR0503-472JL
18 | L3 |  | 1 |  | 74479776247 | L_0805_2012Metric_Pad1.15x1.50mm_HandSolder |  | 74479776247
19 | P1 |  | 1 |  | 691322110005 | WE-3221 - 3.50MM |  | POWER I/O
20 | R1, R2, R3 |  | 3 |  | ERA-6AEB101V | R_0805_2012Metric_Pad1.15x1.50mm_HandSolder |  | 100
21 | R4, R5 |  | 2 |  | ERA-6AEB222V | R_0805_2012Metric_Pad1.15x1.50mm_HandSolder |  | 2.2K
22 | R6, R7 |  | 2 |  | RR1220P-103-D | R_0805_2012Metric_Pad1.15x1.50mm_HandSolder |  | 10K
23 | R8, R22, R24 |  | 3 |  | ERA-6AEB101V | R_0805_2012Metric_Pad1.29x1.40mm_HandSolder |  | 100
24 | R10, R11, R12, R13, R14, R15 |  | 6 |  | RCS0805330RFKEA | R_0805_2012Metric_Pad1.15x1.50mm_HandSolder |  | 330
25 | R16, R18 |  | 2 |  | PR01000103309JR500 | R_Axial_DIN0207_L6.3mm_D2.5mm_P10.16mm_Horizontal |  | 33
26 | R17 |  | 1 |  | PR01000103309JR500 | R_Axial_DIN0207_L6.3mm_D2.5mm_P10.16mm_Horizontal |  | 100
27 | R19, R20 |  | 2 |  | ERA-6AEB6043V | R_0805_2012Metric_Pad1.29x1.40mm_HandSolder |  | 604K
28 | R21 |  | 1 |  | RR1220P-103-D | R_0805_2012Metric_Pad1.29x1.40mm_HandSolder |  | 10k
29 | R23 |  | 1 |  | RR1220P-103-D | R_0805_2012Metric_Pad1.29x1.40mm_HandSolder |  | 10K
30 | RV1 |  | 1 |  | B72214S0351K101 | C_Disc_D4.3mm_W1.9mm_P5.00mm |  | B72214S0351K101
31 | SW1 |  | 1 |  | EVQ-PUA02K | Panasonic_EVQPUL_EVQPUC |  | RST
32 | U2 |  | 1 |  | OM-O2P | OMEGA_2 |  | OMEGA_2
33 | U3 |  | 1 |  | TLV1117-33CDCYR | SOT-223 |  | AP111733
34 | U4 |  | 1 |  | PBO-3-S5 | PBO-3-S5 |  | PBO-3-S5
35 | U5, U6, U7 |  | 3 |  | MOC3063S-TA1 | MOC306X |  | MOC3063S-TA1
36 | U8, U9, U10 |  | 3 |  | Z0103MN 5AA4 | SOT-223-Z01 |  | Z0103MN 5AA4
37 | U11 |  | 1 |  | TLA2024IRUGT | PQFP-N10 |  | TLA2024IRUGT
38 | U12 |  | 1 |  | DS1307Z+T&R | SOIC-8_3.9x4.9mm_P1.27mm |  | DS1307Z+
39 | Y1 |  | 1 |  | AB38T-32.768KHZ | Crystal_AT310_D3.0mm_L10.0mm_Horizontal |  | 32.768KHZ

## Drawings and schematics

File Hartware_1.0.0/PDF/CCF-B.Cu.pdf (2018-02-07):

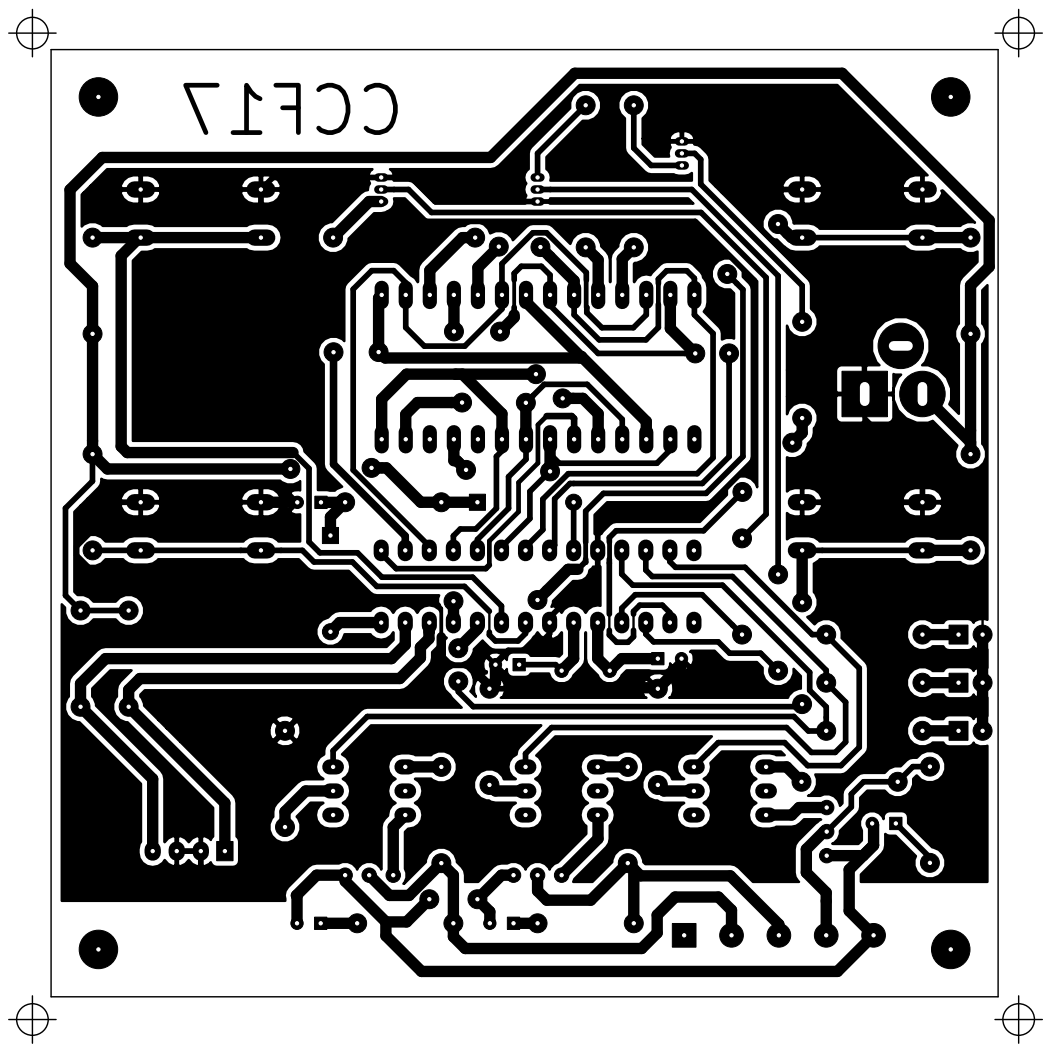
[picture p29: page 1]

File: CCF.kicad_pcb Sheet: ZZI CCF17

Id: 1/1 Title: CONTROL DE CUERTO FRIO

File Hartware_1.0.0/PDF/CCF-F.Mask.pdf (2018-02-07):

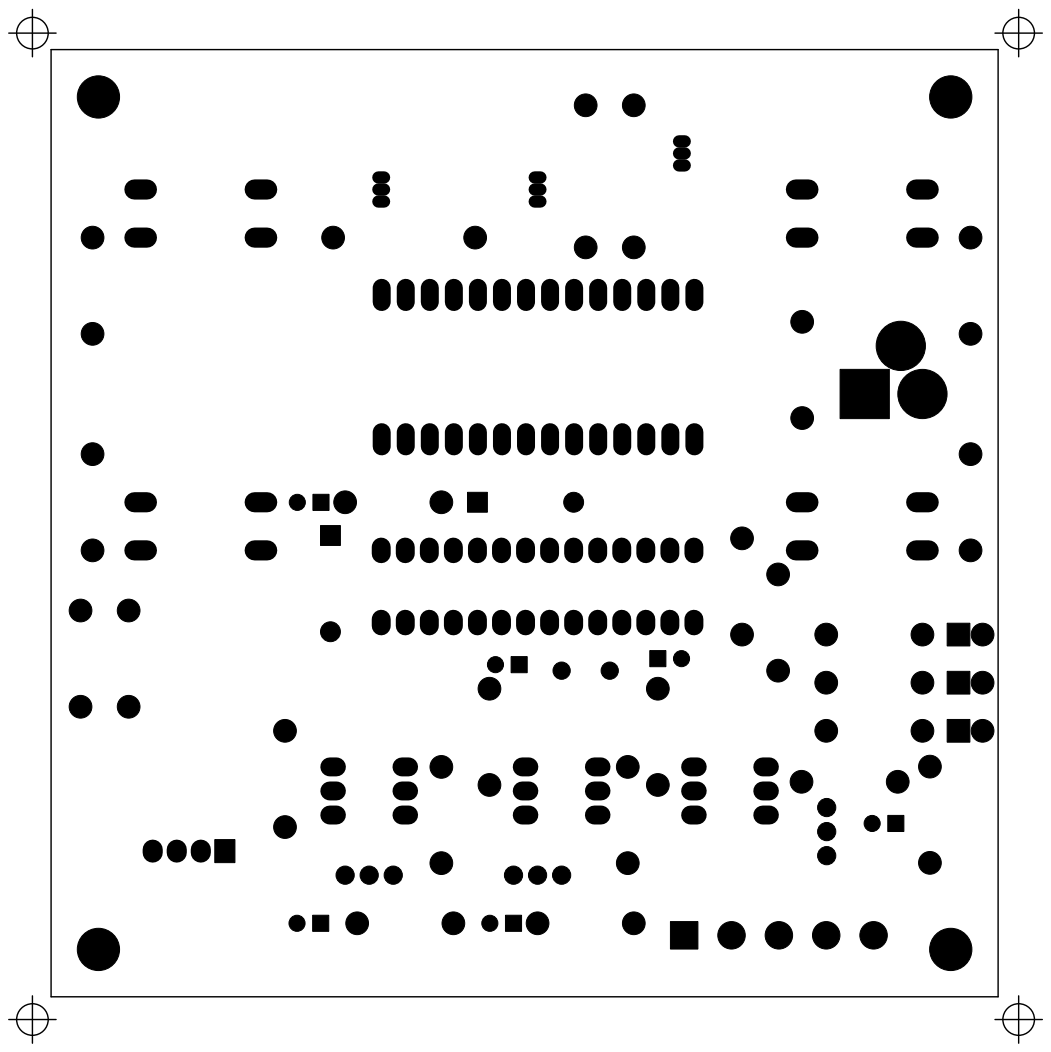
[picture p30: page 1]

File: CCF.kicad_pcb Sheet: ZZI

Id: 1/1 Title: CONTROL DE CUERTO FRIO

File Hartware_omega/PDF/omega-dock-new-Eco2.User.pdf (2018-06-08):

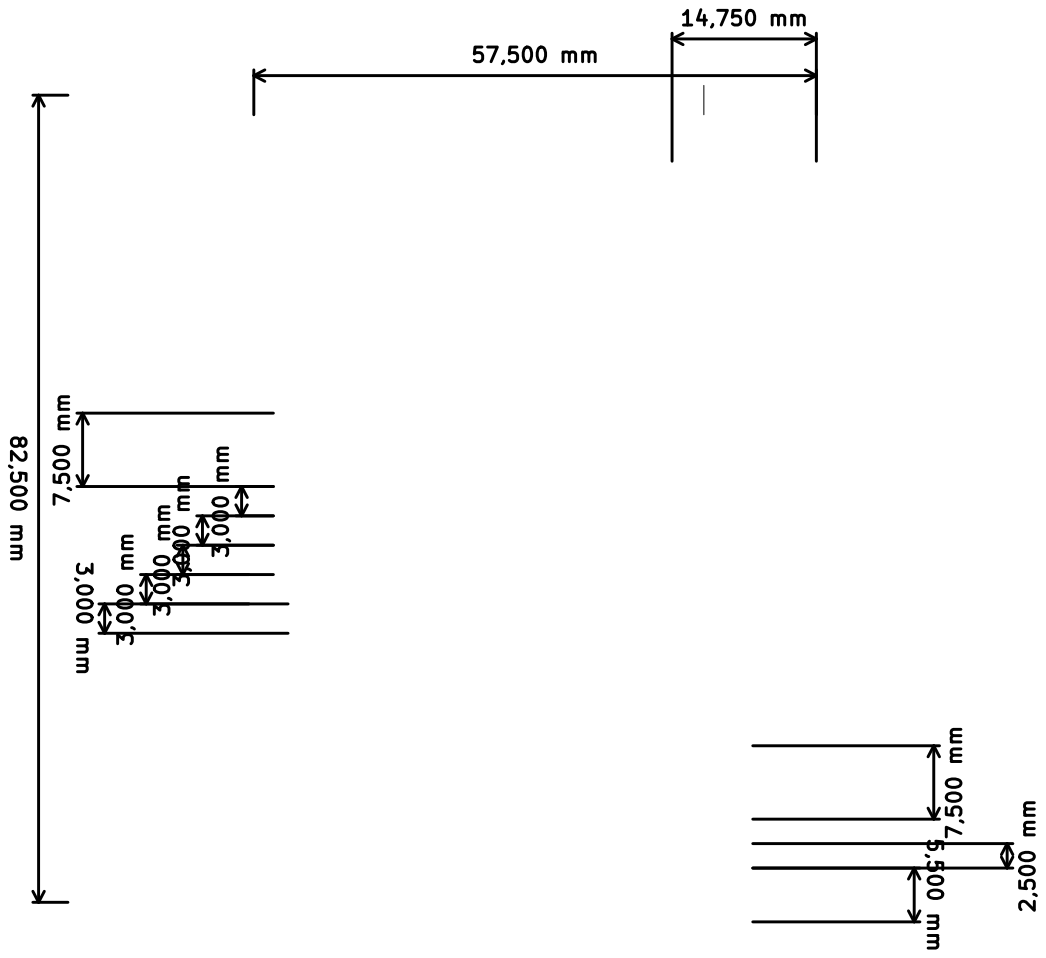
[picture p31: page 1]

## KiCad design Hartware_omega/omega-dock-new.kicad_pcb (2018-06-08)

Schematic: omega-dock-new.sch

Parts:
BT1: 3V; BatteryHolder_Keystone_3000_1x12mm
C1: 22uF; CP_Elec_5x5.3
D1, D2, D3, D4, D6, D7: LED; LED_0603_1608Metric_Castellated
D5: Bridge; MBS -1
J1: SI; HE_XDF1B_1x03_P2.50mm_Horizontal
J2: Termistor; JST_XH_S04B-XH-A-1_1x04_P2.50mm_Horizontal
R1, R2, R3: 100; R_0805_2012Metric_Pad1.15x1.50mm_HandSolder
R4, R5: 2.2K; R_0805_2012Metric_Pad1.15x1.50mm_HandSolder
R6, R7: 10K; R_0805_2012Metric_Pad1.15x1.50mm_HandSolder
R8, R22, R24: 100; R_0805_2012Metric_Pad1.29x1.40mm_HandSolder
R19, R20: 604K; R_0805_2012Metric_Pad1.29x1.40mm_HandSolder
R21: 10k; R_0805_2012Metric_Pad1.29x1.40mm_HandSolder
R23: 10K; R_0805_2012Metric_Pad1.29x1.40mm_HandSolder
SW1: RST; Panasonic_EVQPUL_EVQPUC
U2: OMEGA_2
U11: TLA2024IRUGT; PQFP-N10
U12: DS1307Z+; SOIC-8_3.9x4.9mm_P1.27mm
Y1: 32.768KHZ; Crystal_AT310_D3.0mm_L10.0mm_Horizontal

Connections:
+3V3: R4.1, R5.1, R6.1, R7.1, SW1.1, U2.31, U11.8; also elsewhere on the board
+5V: J1.1, U12.8; also elsewhere on the board
+BATT: BT1.1, U12.3
/GPIO: R24.1, U2.19; also elsewhere on the board
/I_TEST: J1.2, U11.7
/OutTriac/Compresor: D3.2, U2.5; also elsewhere on the board
/OutTriac/Resistencia: D1.2, U2.7; also elsewhere on the board
/OutTriac/Ventilador: D2.2, U2.6; also elsewhere on the board
/SCL: R4.2, U2.18, U11.10, U12.6
/SDA: R5.2, U2.17, U11.9, U12.5
/V_TEST: C1.1, R20.2, R21.1, U11.6; also elsewhere on the board
/error: R22.1, U2.2
/red: R8.1, U2.20
GND: BT1.2, C1.2, D4.1, D5.4, D6.1, D7.1, J1.3, J2.2, J2.4, R1.2, R2.2, R3.2, R21.2, R23.2, U2.1, U2.32, U11.1, U11.3, U12.4; also elsewhere on the board
Nac: D5.2; also elsewhere on the board
unnamed: D1.1, R1.1
unnamed: D2.1, R2.1
unnamed: D3.1, R3.1
unnamed: D4.2, R8.2
unnamed: D5.3, R19.1
unnamed: D6.2, R22.2
unnamed: D7.2, R24.2
unnamed: J2.1, R7.2, U11.4
unnamed: J2.3, R6.2, U11.5
unnamed: R19.2, R20.1
unnamed: R23.1, SW1.2, U2.26
unnamed: U12.1, Y1.1
unnamed: U12.2, Y1.2
VacF: D5.1; also elsewhere on the board

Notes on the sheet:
Omega dock\ new
August 7, 2017
1.0
https://github.com/5N44P/omega-dock-new
address->0x48

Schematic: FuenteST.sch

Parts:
C5, C6: 4,7uF; CP_Radial_D8.0mm_P3.50mm
C7: 10uF; CP_Elec_4x5.3
C8: 1nF; C_0805_2012Metric_Pad1.15x1.50mm_HandSolder
C9: 100uF; CP_Elec_4x5.3
C10: 270uF; CP_Elec_6.3x7.7
C11: 68uF; CP_Elec_6.3x7.7
C12: 100nF; C_1206_3216Metric_Pad1.24x1.80mm_HandSolder
F1: 1A; FC-211-22_M
L2: SDR0503-472JL; SDR0503-XXX
L3: 74479776247; L_0805_2012Metric_Pad1.15x1.50mm_HandSolder
RV1: B72214S0351K101; C_Disc_D4.3mm_W1.9mm_P5.00mm
U3: AP111733; SOT-223
U4: PBO-3-S5

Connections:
+3V3: C9.1, U3.2 (VO), U3.4 (VO); also elsewhere on the board
+5V: C7.1, C11.1, C12.1, L3.2, U3.3 (VI); also elsewhere on the board
/FuenteST/VO: C10.1, L3.1, U4.12
GND: C7.2, C8.2, C9.2, C10.2, C11.2, C12.2, U3.1 (GND), U4.10; also elsewhere on the board
Nac: RV1.2, U4.1; also elsewhere on the board
unnamed: C5.1, C6.1, U4.5
unnamed: C5.2, C6.2, C8.1, U4.7
unnamed: L2.2, U4.3
Vac: F1.2; also elsewhere on the board
VacF: F1.1, L2.1, RV1.1; also elsewhere on the board

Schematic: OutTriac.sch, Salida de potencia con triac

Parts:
C13, C14, C15: 1nF; C_Rect_L13.0mm_W4.0mm_P10.00mm_FKS3_FKP3_MKS4
P1: POWER I/O; WE-3221 - 3.50MM
R10, R11, R12, R13, R14, R15: 330; R_0805_2012Metric_Pad1.15x1.50mm_HandSolder
R16, R18: 33; R_Axial_DIN0207_L6.3mm_D2.5mm_P10.16mm_Horizontal
R17: 100; R_Axial_DIN0207_L6.3mm_D2.5mm_P10.16mm_Horizontal
U5, U6, U7: MOC3063S-TA1; MOC306X
U8, U9, U10: Z0103MN 5AA4; SOT-223-Z01

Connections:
/OutTriac/Compresor: U7.1; also elsewhere on the board
/OutTriac/Resistencia: U6.1; also elsewhere on the board
/OutTriac/Ventilador: U5.1; also elsewhere on the board
CO: P1.4, R15.1, R18.1, U10.2
GND: R10.2, R11.2, R12.2; also elsewhere on the board
Nac: C13.2, C14.2, C15.2, P1.1, U8.1, U9.1, U10.1; also elsewhere on the board
unnamed: C13.1, R16.2
unnamed: C14.1, R17.2
unnamed: C15.1, R18.2
unnamed: R10.1, U5.2
unnamed: R11.1, U6.2
unnamed: R12.1, U7.2
unnamed: R13.2, U5.6
unnamed: R14.2, U6.6
unnamed: R15.2, U7.6
unnamed: U5.4, U8.3
unnamed: U6.4, U9.3
unnamed: U7.4, U10.3
RE: P1.3, R14.1, R17.1, U9.2
VE: P1.2, R13.1, R16.1, U8.2
Vac: P1.5; also elsewhere on the board

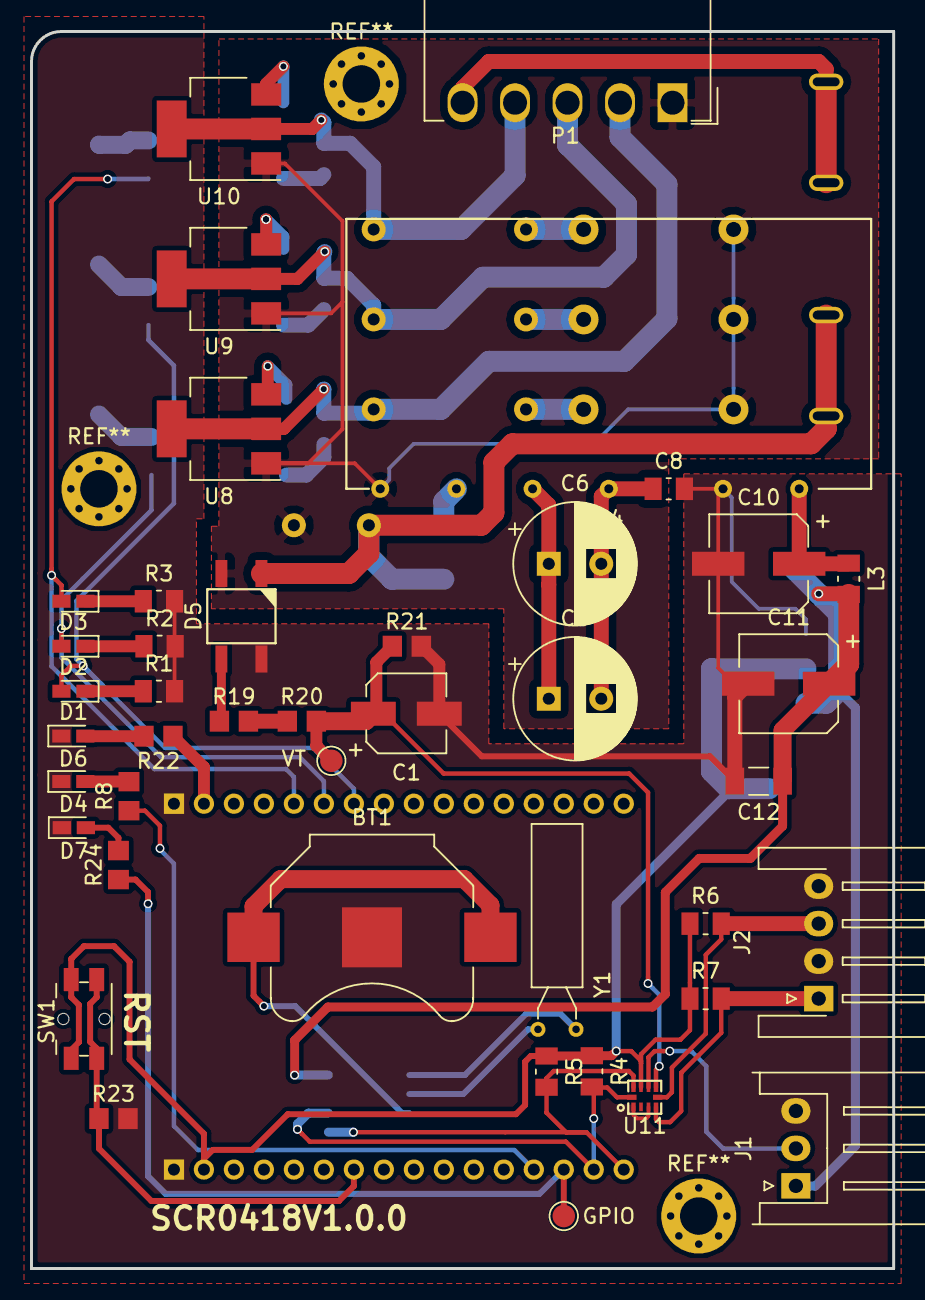
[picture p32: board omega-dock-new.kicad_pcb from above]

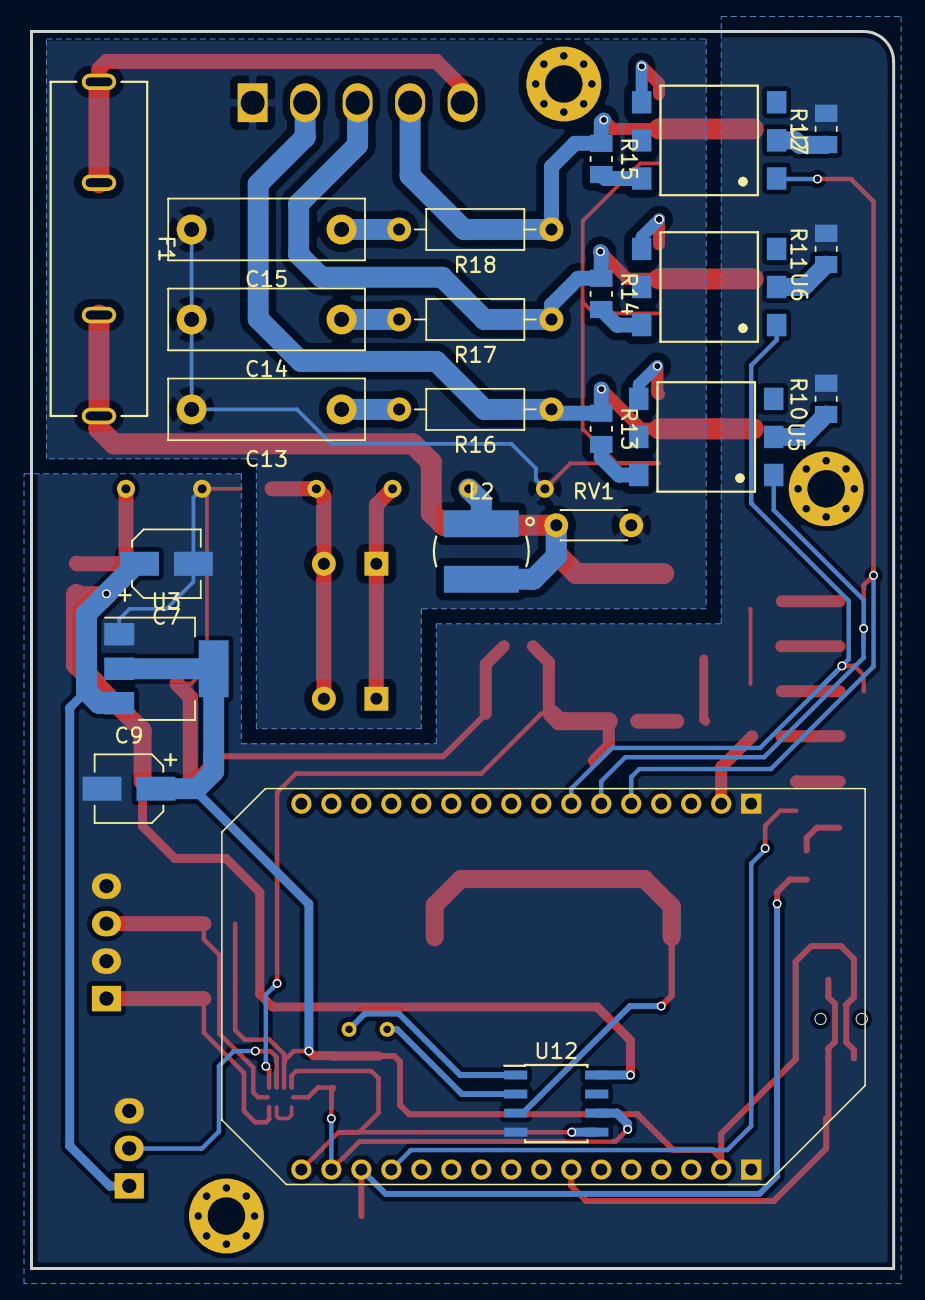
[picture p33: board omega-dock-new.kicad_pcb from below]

Board: 2 copper layers, 57.5 x 82.5 mm, 65 parts (23 on the bottom side), 49 nets.

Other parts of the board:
GPIO: TestPoint_Pad_D1.5mm
VT: TestPoint_Pad_D1.5mm

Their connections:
/GPIO: GPIO.1; also elsewhere on the board
/V_TEST: VT.1; also elsewhere on the board

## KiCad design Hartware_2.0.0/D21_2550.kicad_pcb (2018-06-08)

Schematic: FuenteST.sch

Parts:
C1, C11: 4,7uF; CP_Radial_D8.0mm_P3.50mm
C8: 1nF; C_0805_2012Metric_Pad1.15x1.50mm_HandSolder
C9: 270uF; CP_Elec_6.3x7.7
C10: 68uF; CP_Elec_6.3x7.7
C12: 100nF; C_1206_3216Metric_Pad1.24x1.80mm_HandSolder
L1: SDR0503-472JL; SDR0503-XXX
L2: 74479776247; L_0805_2012Metric_Pad1.15x1.50mm_HandSolder
R1: 300k; R_1206_3216Metric_Pad1.24x1.80mm_HandSolder
RV1: B72214S0351K101; C_Disc_D4.3mm_W1.9mm_P5.00mm
U8: PBO-3-S5

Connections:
/Fuente/VO: C9.1, L2.1, U8.12
GND: C8.2, C9.2, C10.2, C12.2, U8.10; also elsewhere on the board
Nac: RV1.2, U8.1; also elsewhere on the board
unnamed: C1.1, C11.1, U8.5
unnamed: C1.2, C8.1, C11.2, U8.7
unnamed: L1.1, R1.1
unnamed: L1.2, U8.3
VDD: C10.1, C12.1, L2.2; also elsewhere on the board
Vac: R1.2, RV1.1; also elsewhere on the board

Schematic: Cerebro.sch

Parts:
C2, C3: 33pf; C_0805_2012Metric_Pad1.15x1.50mm_HandSolder
D8, D9, D10: LED; LED_0603_1608Metric_Pad0.67x1.00mm_HandSolder
JP1: pgm; PinHeader_1x02_P2.54mm_Vertical
P4: ISCP; PinHeader_1x05_P2.54mm_Vertical
R2: 10k; R_0805_2012Metric_Pad1.15x1.50mm_HandSolder
R24, R25, R26: 220; R_0805_2012Metric_Pad1.15x1.50mm_HandSolder
U1: PIC18F2550-ISO; SOIC-28W_7.5x17.9mm_P1.27mm
Y1: 20MHZ; Crystal_SMD_ABLS_HC49-SD

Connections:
/Cerebro/7 SEGMENTOS/A: U1.21 (RB0/AN12/INT0/FLT0/SDI/SDA); also elsewhere on the board
/Cerebro/7 SEGMENTOS/B: U1.22 (RB1/AN10/INT1/SCK/SCL); also elsewhere on the board
/Cerebro/7 SEGMENTOS/C: U1.23 (RB2/AN8/INT2/VMO); also elsewhere on the board
/Cerebro/7 SEGMENTOS/D: U1.24 (RB3/AN9/CCP2/VPO); also elsewhere on the board
/Cerebro/7 SEGMENTOS/E: U1.25 (RB4/AN11/KBI0); also elsewhere on the board
/Cerebro/7 SEGMENTOS/E1: U1.11 (T1OSO/T13CKI/RC0); also elsewhere on the board
/Cerebro/7 SEGMENTOS/E2: U1.12 (~UOE~/CCP2/T1OSI/RC1); also elsewhere on the board
/Cerebro/7 SEGMENTOS/E3: U1.13 (CCP1/RC2); also elsewhere on the board
/Cerebro/7 SEGMENTOS/F: U1.26 (RB5/KBI1/PGM); also elsewhere on the board
/Cerebro/Acond NTC/T_A: U1.3 (RA1/AN1); also elsewhere on the board
/Cerebro/Acond NTC/T_R: U1.2 (RA0/AN0); also elsewhere on the board
/Cerebro/Botones/+: U1.6 (RA4/T0CKI/C1OUT/RCV); also elsewhere on the board
/Cerebro/Botones/-: U1.7 (RA5/AN4/~SS~/HLVDIN/C2OUT); also elsewhere on the board
/Cerebro/Botones/P: U1.4 (RA2/AN2/Vref-/CVref); also elsewhere on the board
/Cerebro/Botones/S: U1.5 (RA3/AN3/Vref+); also elsewhere on the board
/Cerebro/Salida de potencia/Compresor: R24.1, U1.16 (VP/D+/RC5); also elsewhere on the board
/Cerebro/Salida de potencia/Resistencia: R26.1, U1.18 (SDO/RX/DT/RC7); also elsewhere on the board
/Cerebro/Salida de potencia/Ventilador: R25.1, U1.17 (TX/CK/RC6); also elsewhere on the board
GND: C2.2, C3.2, D8.1, D9.1, D10.1, P4.3, U1.8 (VSS), U1.19 (VSS); also elsewhere on the board
K1: C2.1, U1.10 (RA6/OSC2/CLKO), Y1.1
K2: C3.1, U1.9 (OSC1/CLKI), Y1.2
unnamed: D8.2, R24.2
unnamed: D9.2, R25.2
unnamed: D10.2, R26.2
PGC: P4.1, U1.27 (RB6/KBI2/PGC); also elsewhere on the board
PGD: P4.2, U1.28 (RB7/KBI3/PGD); also elsewhere on the board
VDD: JP1.1, R2.1; also elsewhere on the board
VDDP: JP1.2, P4.4, U1.20 (VDD); also elsewhere on the board
VPP: P4.5, R2.2, U1.1 (Vpp/~MCLR~/RE3)

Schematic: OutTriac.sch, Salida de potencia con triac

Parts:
C4, C5, C6: 1nF; C_Rect_L13.0mm_W4.0mm_P10.00mm_FKS3_FKP3_MKS4
P1: POWER I/O; TerminalBlock_bornier-5_P5.08mm
R3, R4, R5, R6, R7, R8: 330; R_0805_2012Metric_Pad1.15x1.50mm_HandSolder
R9, R10: 33; R_Axial_DIN0207_L6.3mm_D2.5mm_P10.16mm_Horizontal
R11: 100; R_Axial_DIN0207_L6.3mm_D2.5mm_P10.16mm_Horizontal
U2, U3, U4: MOC3063S-TA1; MOC306X
U5, U6, U7: Z0103MN 5AA4; SOT-223-Z01

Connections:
/Cerebro/Salida de potencia/Compresor: U2.1; also elsewhere on the board
/Cerebro/Salida de potencia/Resistencia: U4.1; also elsewhere on the board
/Cerebro/Salida de potencia/Ventilador: U3.1; also elsewhere on the board
CO: P1.2, R6.1, R9.1, U5.2
GND: R3.2, R4.2, R5.2; also elsewhere on the board
Nac: C4.2, C5.2, C6.2, P1.5, U5.1, U6.1, U7.1; also elsewhere on the board
unnamed: C4.1, R9.2
unnamed: C5.1, R10.2
unnamed: C6.1, R11.2
unnamed: R3.1, U2.2
unnamed: R4.1, U3.2
unnamed: R5.1, U4.2
unnamed: R6.2, U2.6
unnamed: R7.2, U3.6
unnamed: R8.2, U4.6
unnamed: U2.4, U5.3
unnamed: U3.4, U6.3
unnamed: U4.4, U7.3
RE: P1.4, R8.1, R11.1, U7.2
VE: P1.3, R7.1, R10.1, U6.2
Vac: P1.1; also elsewhere on the board

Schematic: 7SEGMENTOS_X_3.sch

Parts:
D11: LTC-4724JR
Q1, Q2, Q3: FZT493TA; SOT-223
R12, R13, R14: 2.7k; R_0805_2012Metric_Pad1.15x1.50mm_HandSolder
R15, R16, R17: 22; R_2512_6332Metric_Pad1.34x3.40mm_HandSolder

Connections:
/Cerebro/7 SEGMENTOS/A: D11.12; also elsewhere on the board
/Cerebro/7 SEGMENTOS/B: D11.11; also elsewhere on the board
/Cerebro/7 SEGMENTOS/C: D11.3; also elsewhere on the board
/Cerebro/7 SEGMENTOS/D: D11.4; also elsewhere on the board
/Cerebro/7 SEGMENTOS/E: D11.2; also elsewhere on the board
/Cerebro/7 SEGMENTOS/E1: R12.2; also elsewhere on the board
/Cerebro/7 SEGMENTOS/E2: R13.2; also elsewhere on the board
/Cerebro/7 SEGMENTOS/E3: R14.2; also elsewhere on the board
/Cerebro/7 SEGMENTOS/F: D11.15; also elsewhere on the board
GND: Q1.3, Q2.3, Q3.3; also elsewhere on the board
unnamed: D11.1, R15.2
unnamed: D11.5, R16.2
unnamed: D11.7, R17.2
unnamed: Q1.1, R15.1
unnamed: Q1.2, R12.1
unnamed: Q2.1, R16.1
unnamed: Q2.2, R13.1
unnamed: Q3.1, R17.1
unnamed: Q3.2, R14.1
PGC: D11.8; also elsewhere on the board
PGD: D11.6; also elsewhere on the board

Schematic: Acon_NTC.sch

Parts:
J1: THR; JST_XH_S04B-XH-A-1_1x04_P2.50mm_Horizontal
R18, R19: 20k; R_0805_2012Metric_Pad1.15x1.50mm_HandSolder

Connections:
/Cerebro/Acond NTC/T_A: J1.4, R18.2; also elsewhere on the board
/Cerebro/Acond NTC/T_R: J1.2, R19.2; also elsewhere on the board
GND: J1.1, J1.3; also elsewhere on the board
VDD: R18.1, R19.1; also elsewhere on the board

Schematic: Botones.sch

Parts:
R20, R21, R22, R23: 10k; R_0805_2012Metric_Pad1.15x1.50mm_HandSolder
SW1, SW2, SW3, SW4: TL3301AF160QG

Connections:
/Cerebro/Botones/+: R20.2, SW1.2; also elsewhere on the board
/Cerebro/Botones/-: R21.2, SW2.2; also elsewhere on the board
/Cerebro/Botones/P: R22.2, SW3.1; also elsewhere on the board
/Cerebro/Botones/S: R23.2, SW4.1; also elsewhere on the board
GND: SW1.1, SW2.1, SW3.2, SW4.2; also elsewhere on the board
VDD: R20.1, R21.1, R22.1, R23.1; also elsewhere on the board

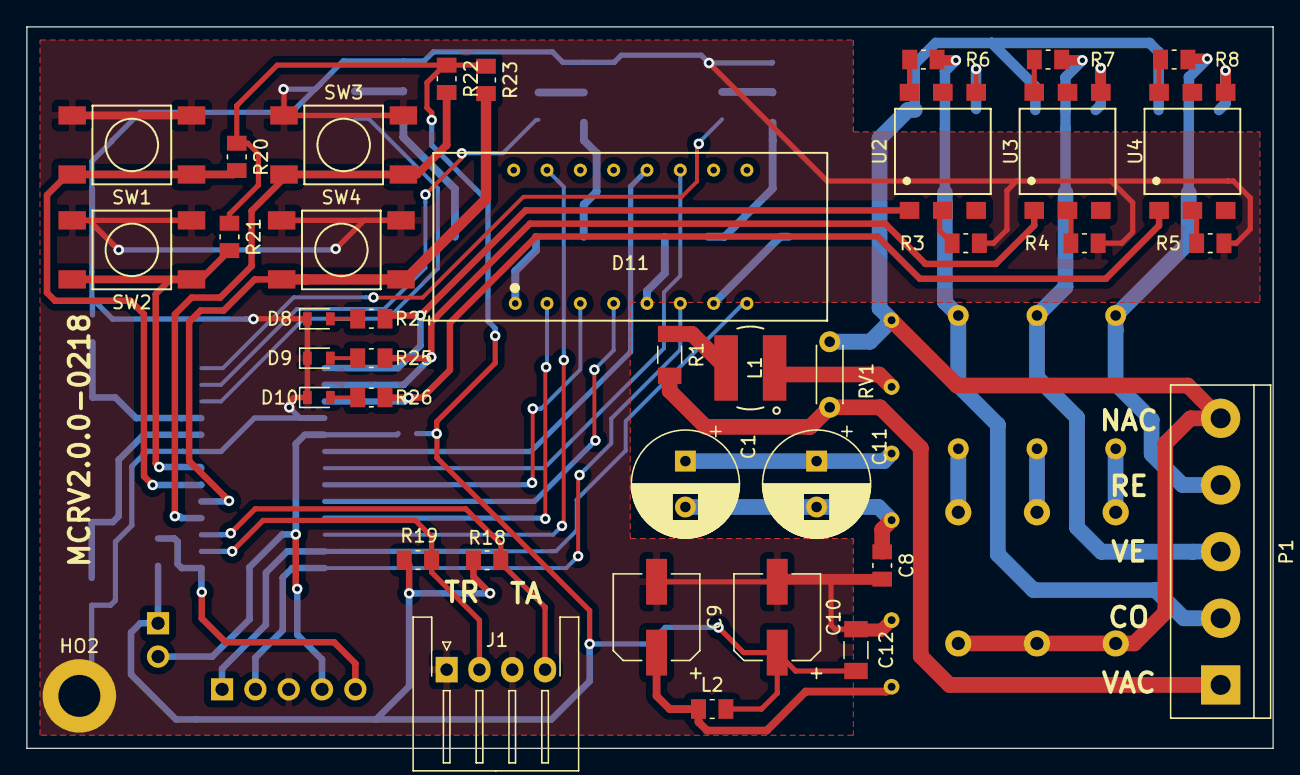
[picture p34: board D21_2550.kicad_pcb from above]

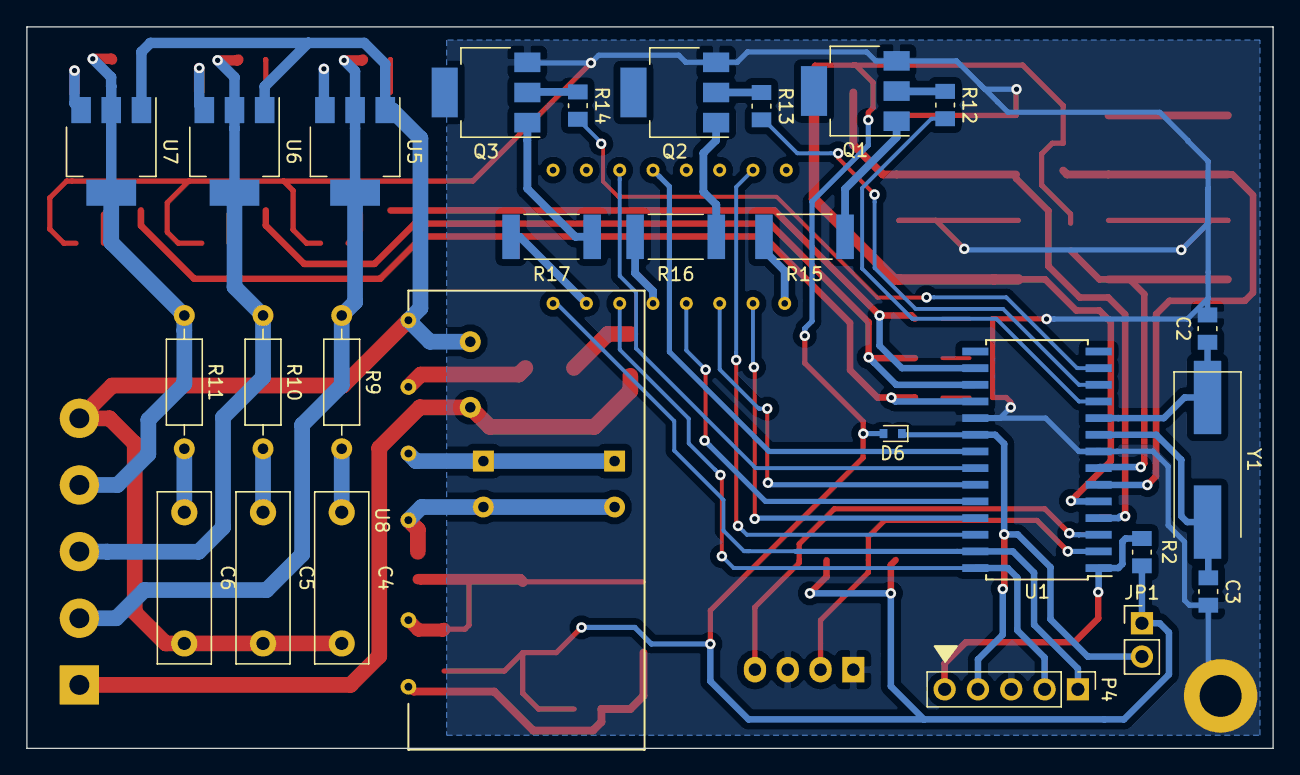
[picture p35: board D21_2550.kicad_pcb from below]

Board: 2 copper layers, 95.0 x 55.0 mm, 66 parts (27 on the bottom side), 60 nets.

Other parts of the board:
D6: 1N4148X-TP; D_SOD-523
HO2: MountingHole_3.2mm_M3_DIN965_Pad

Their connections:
GND: HO2.1; also elsewhere on the board
VDD: D6.2; also elsewhere on the board
VDDP: D6.1; also elsewhere on the board

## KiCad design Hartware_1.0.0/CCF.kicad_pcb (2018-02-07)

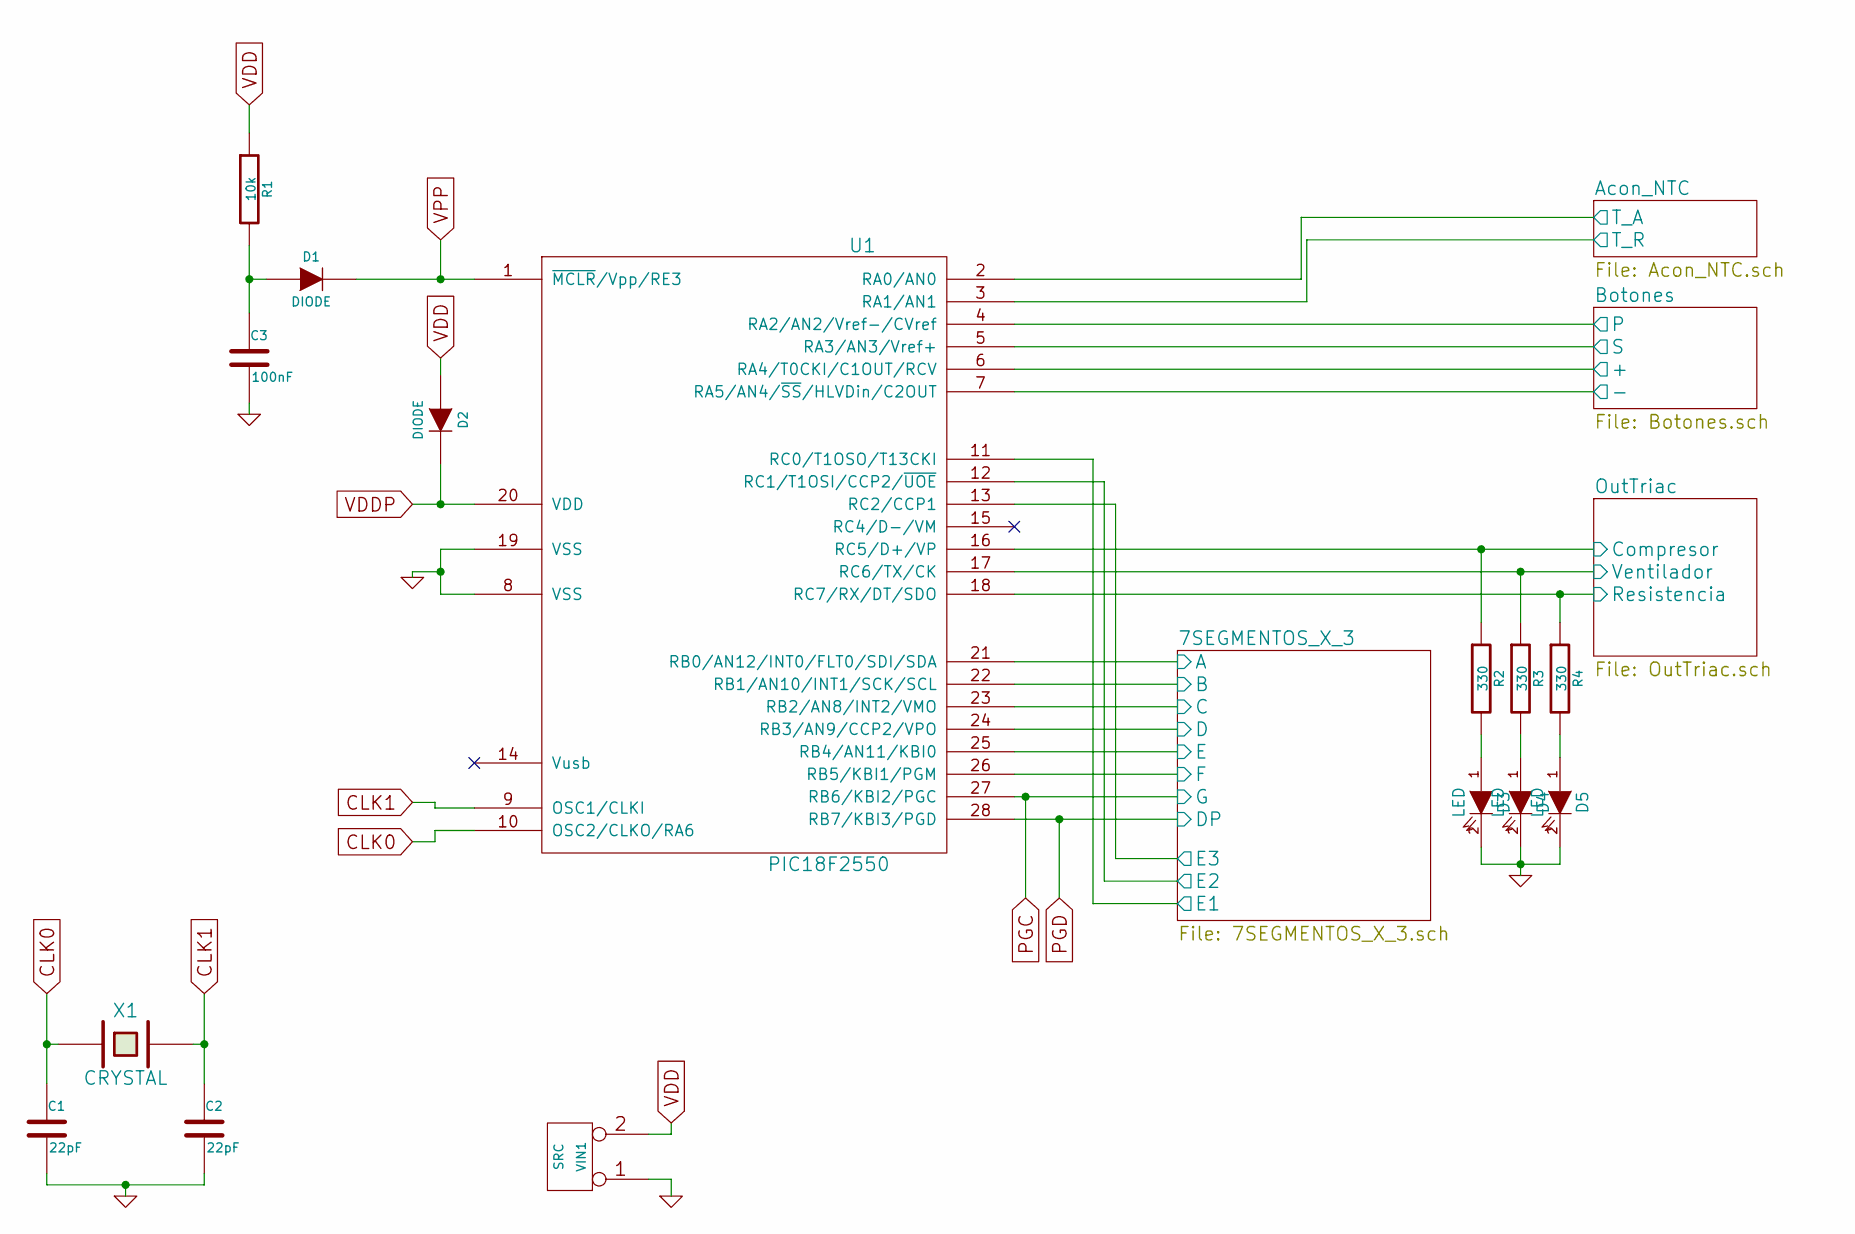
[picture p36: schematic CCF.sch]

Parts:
C1, C2: 22pF; C_Disc_D3_P2.5
C3: 100nF; C_Disc_D3_P2.5
D1, D2: DIODE; Diode_DO-35_SOD27_Horizontal_RM10
D3, D4, D5: LED; LED-3MM
R1: 10k; Resistor_Horizontal_RM10mm
R2, R3, R4: 330; Resistor_Horizontal_RM10mm
U1: PIC18F2550; DIP-28_W7.62mm_LongPads
VIN1: SRC; JACK_ALIM
X1: CRYSTAL; HC-49V

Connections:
/7SEGMENTOS_X_3/A: U1.21 (RB0/AN12/INT0/FLT0/SDI/SDA); also elsewhere on the board
/7SEGMENTOS_X_3/B: U1.22 (RB1/AN10/INT1/SCK/SCL); also elsewhere on the board
/7SEGMENTOS_X_3/C: U1.23 (RB2/AN8/INT2/VMO); also elsewhere on the board
/7SEGMENTOS_X_3/D: U1.24 (RB3/AN9/CCP2/VPO); also elsewhere on the board
/7SEGMENTOS_X_3/E: U1.25 (RB4/AN11/KBI0); also elsewhere on the board
/7SEGMENTOS_X_3/E1: U1.11 (RC0/T1OSO/T13CKI); also elsewhere on the board
/7SEGMENTOS_X_3/E2: U1.12 (RC1/T1OSI/CCP2/~UOE); also elsewhere on the board
/7SEGMENTOS_X_3/E3: U1.13 (RC2/CCP1); also elsewhere on the board
/7SEGMENTOS_X_3/F: U1.26 (RB5/KBI1/PGM); also elsewhere on the board
/Acon_NTC/T_A: U1.2 (RA0/AN0); also elsewhere on the board
/Acon_NTC/T_R: U1.3 (RA1/AN1); also elsewhere on the board
/Botones/+: U1.6 (RA4/T0CKI/C1OUT/RCV); also elsewhere on the board
/Botones/-: U1.7 (RA5/AN4/~SS~/HLVDin/C2OUT); also elsewhere on the board
/Botones/P: U1.4 (RA2/AN2/Vref-/CVref); also elsewhere on the board
/Botones/S: U1.5 (RA3/AN3/Vref+); also elsewhere on the board
/OutTriac/Compresor: R2.1, U1.16 (RC5/D+/VP); also elsewhere on the board
/OutTriac/Resistencia: R4.1, U1.18 (RC7/RX/DT/SDO); also elsewhere on the board
/OutTriac/Ventilador: R3.1, U1.17 (RC6/TX/CK); also elsewhere on the board
CLK0: C1.1, U1.10 (OSC2/CLKO/RA6), X1.1
CLK1: C2.1, U1.9 (OSC1/CLKI), X1.2
GND: C1.2, C2.2, C3.2, D3.2 (K), D4.2 (K), D5.2 (K), U1.8 (VSS), U1.19 (VSS), VIN1.1; also elsewhere on the board
unnamed: C3.1, D1.1 (A), R1.2
unnamed: D3.1 (A), R2.2
unnamed: D4.1 (A), R3.2
unnamed: D5.1 (A), R4.2
PGC: U1.27 (RB6/KBI2/PGC); also elsewhere on the board
PGD: U1.28 (RB7/KBI3/PGD); also elsewhere on the board
VDD: D2.1 (A), R1.1, VIN1.2 (PM); also elsewhere on the board
VDDP: D2.2 (K), U1.20 (VDD)
VPP: D1.2 (K), U1.1 (~MCLR~/Vpp/RE3)

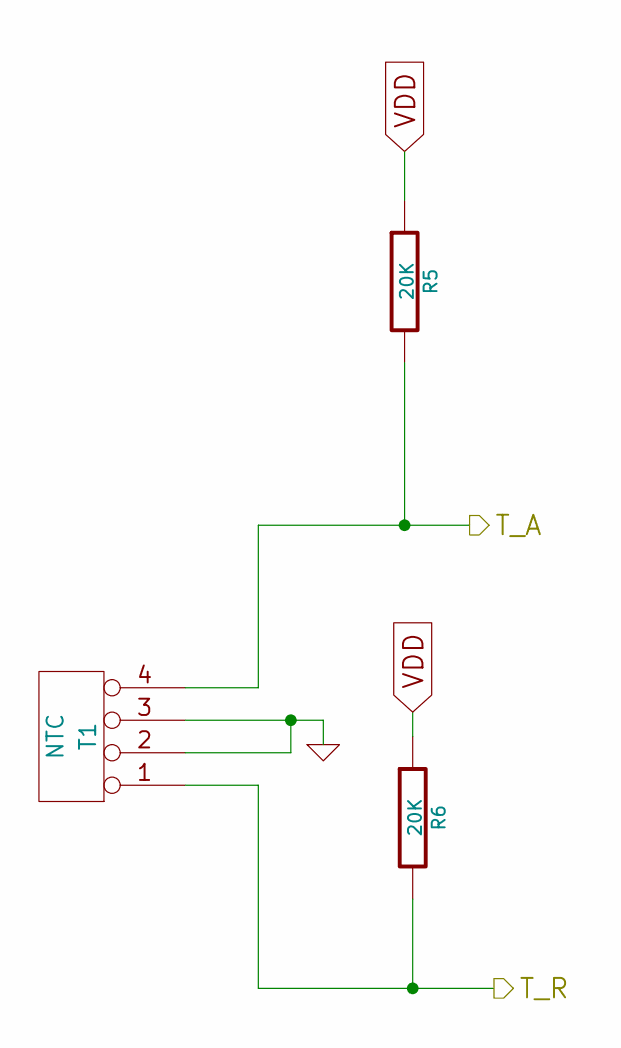
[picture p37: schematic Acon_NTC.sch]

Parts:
R5, R6: 20K; Resistor_Horizontal_RM10mm
T1: NTC; Socket_Strip_Straight_1x04

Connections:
/Acon_NTC/T_A: R5.2, T1.4; also elsewhere on the board
/Acon_NTC/T_R: R6.2, T1.1; also elsewhere on the board
GND: T1.2, T1.3; also elsewhere on the board
VDD: R5.1, R6.1; also elsewhere on the board

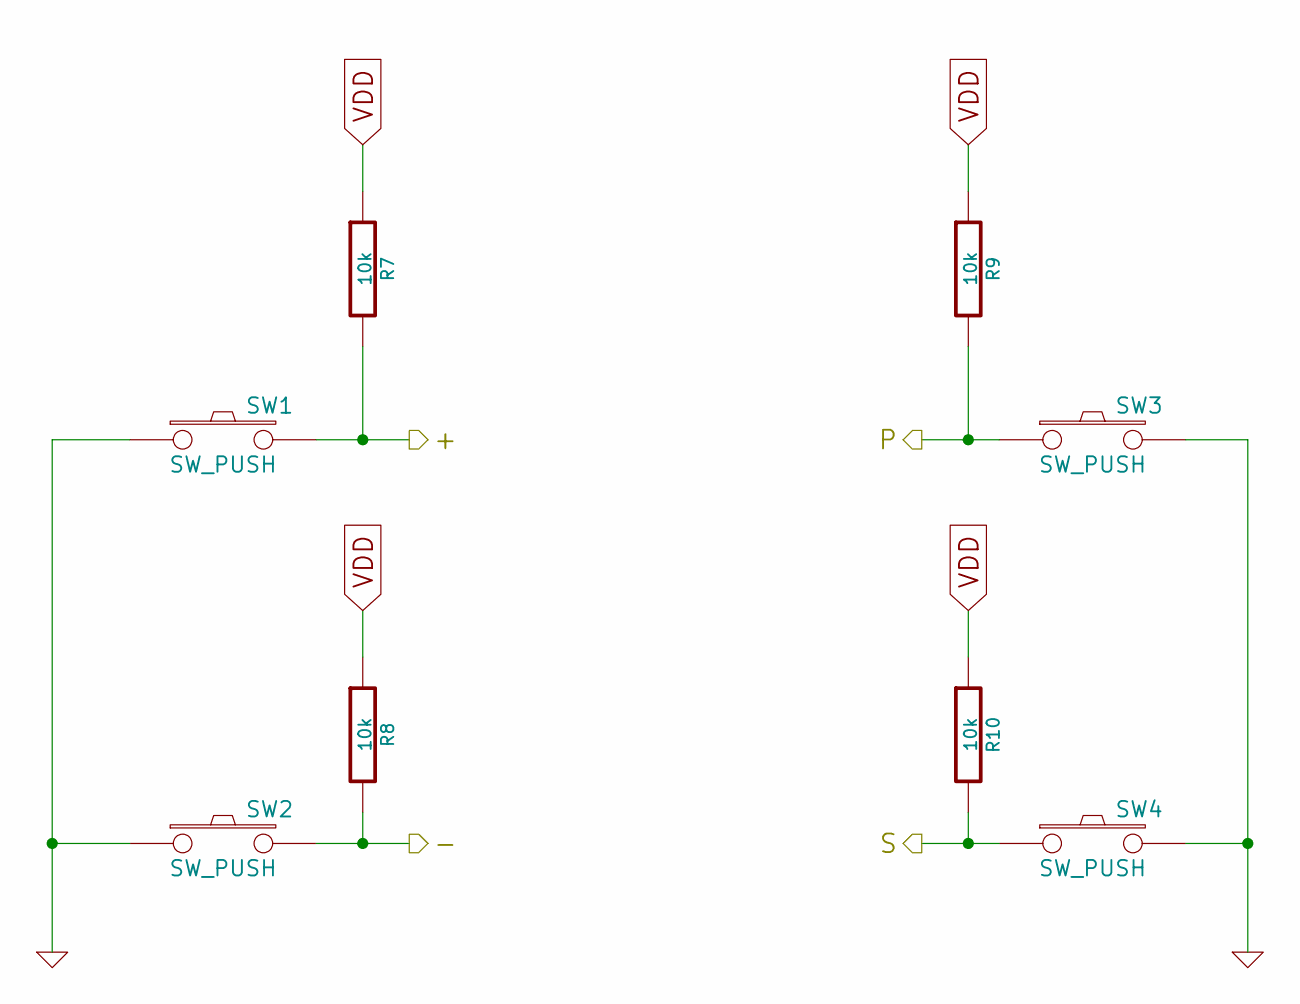
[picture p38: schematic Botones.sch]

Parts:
R7, R8, R9, R10: 10k; Resistor_Horizontal_RM10mm
SW1, SW2, SW3, SW4: SW_PUSH; SW_PUSH-12mm

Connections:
/Botones/+: R7.2, SW1.2; also elsewhere on the board
/Botones/-: R8.2, SW2.2; also elsewhere on the board
/Botones/P: R9.2, SW3.1; also elsewhere on the board
/Botones/S: R10.2, SW4.1; also elsewhere on the board
GND: SW1.1, SW2.1, SW3.2, SW4.2; also elsewhere on the board
VDD: R7.1, R8.1, R9.1, R10.1; also elsewhere on the board

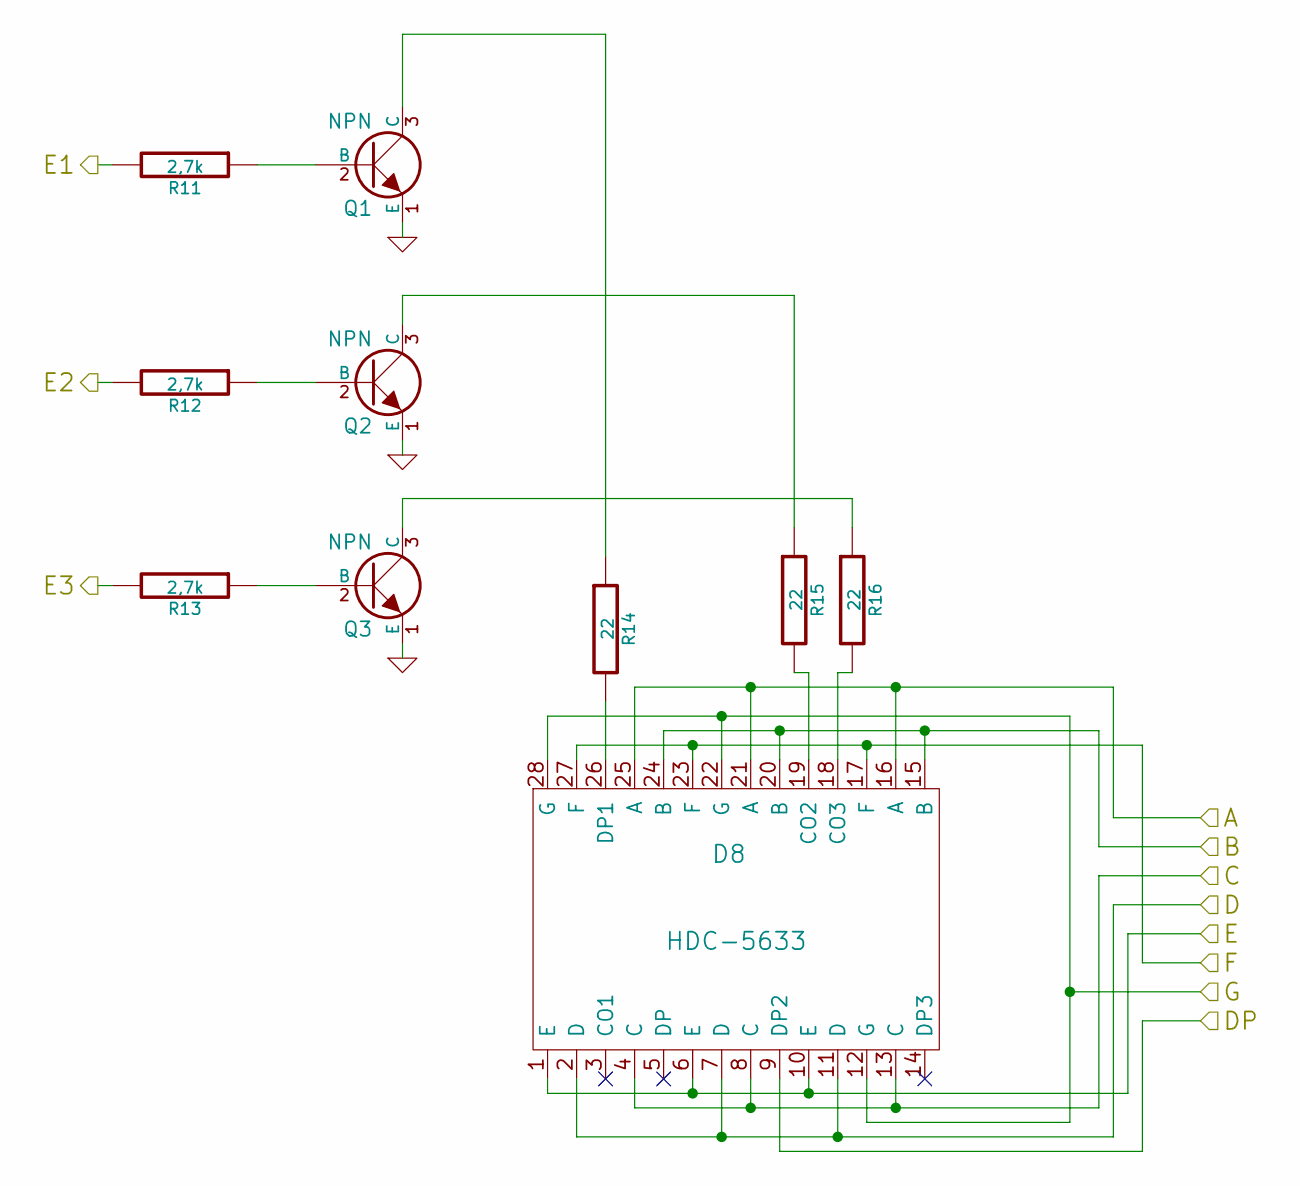
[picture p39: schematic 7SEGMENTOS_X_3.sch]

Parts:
D8: HDC-5633; 7seg-HDC-19x37.5mm
Q1, Q2, Q3: NPN; TO-92_Inline_Narrow_Oval
R11, R12, R13: 2,7k; Resistor_Horizontal_RM10mm
R14, R15, R16: 22; Resistor_Horizontal_RM15mm

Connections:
/7SEGMENTOS_X_3/A: D8.16 (A), D8.21 (A), D8.25 (A); also elsewhere on the board
/7SEGMENTOS_X_3/B: D8.15 (B), D8.20 (B), D8.24 (B); also elsewhere on the board
/7SEGMENTOS_X_3/C: D8.4 (C), D8.8 (C), D8.13 (C); also elsewhere on the board
/7SEGMENTOS_X_3/D: D8.2 (D), D8.7 (D), D8.11 (D); also elsewhere on the board
/7SEGMENTOS_X_3/E: D8.1 (E), D8.6 (E), D8.10 (E); also elsewhere on the board
/7SEGMENTOS_X_3/E1: R11.2; also elsewhere on the board
/7SEGMENTOS_X_3/E2: R12.2; also elsewhere on the board
/7SEGMENTOS_X_3/E3: R13.2; also elsewhere on the board
/7SEGMENTOS_X_3/F: D8.17 (F), D8.23 (F), D8.27 (F); also elsewhere on the board
GND: Q1.1 (E), Q2.1 (E), Q3.1 (E); also elsewhere on the board
unnamed: D8.18 (CO3), R16.2
unnamed: D8.19 (CO2), R15.2
unnamed: D8.26 (DP1), R14.2
unnamed: Q1.2 (B), R11.1
unnamed: Q1.3 (C), R14.1
unnamed: Q2.2 (B), R12.1
unnamed: Q2.3 (C), R15.1
unnamed: Q3.2 (B), R13.1
unnamed: Q3.3 (C), R16.1
PGC: D8.12 (G), D8.22 (G), D8.28 (G); also elsewhere on the board
PGD: D8.9 (DP2); also elsewhere on the board

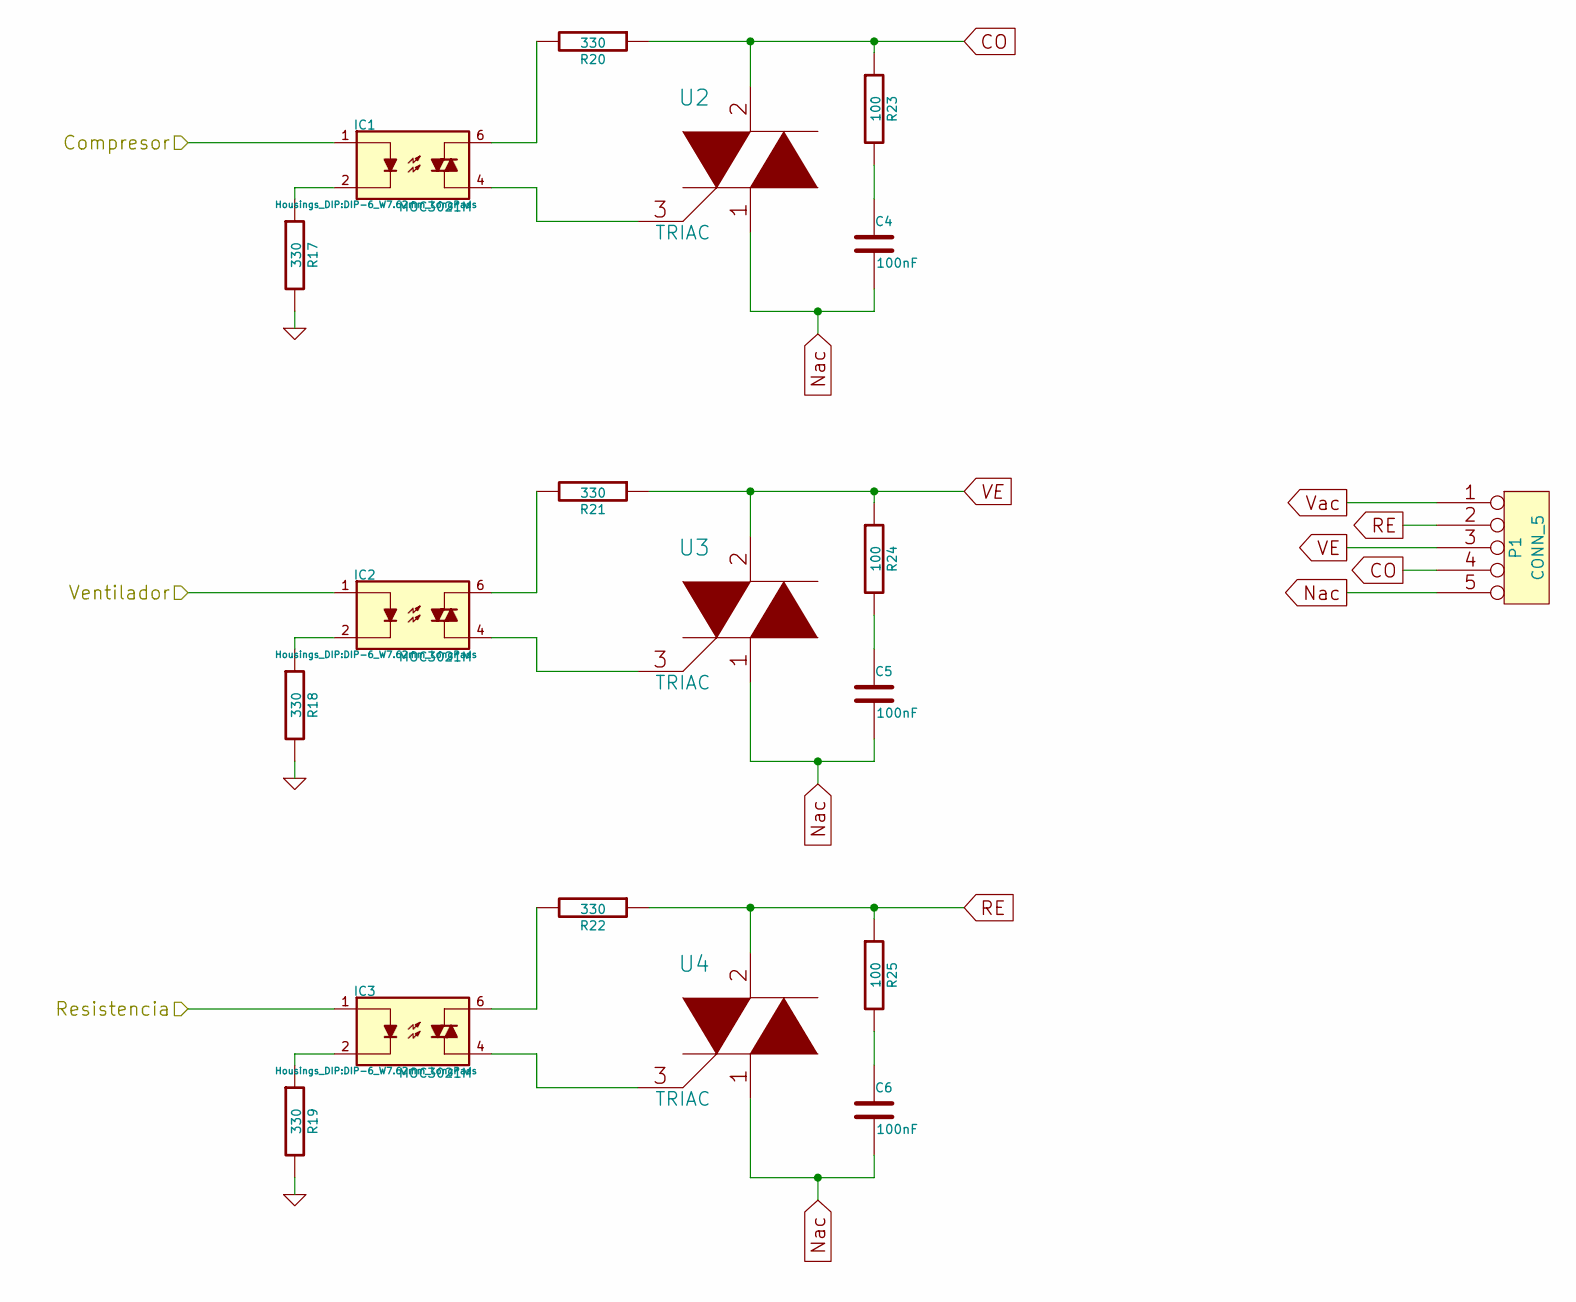
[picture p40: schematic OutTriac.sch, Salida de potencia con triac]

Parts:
C4, C5, C6: 100nF; C_Disc_D3_P2.5
IC1, IC2, IC3: MOC3021M; DIP-6_W7.62mm_LongPads
P1: CONN_5; TerminalBlock_Pheonix_MKDS1.5-5pol
R17, R18, R19, R20, R21, R22: 330; Resistor_Horizontal_RM10mm
R23, R24, R25: 100; Resistor_Horizontal_RM10mm
U2, U3, U4: TRIAC; TO-92_Inline_Wide

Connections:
/OutTriac/Compresor: IC1.1; also elsewhere on the board
/OutTriac/Resistencia: IC3.1; also elsewhere on the board
/OutTriac/Ventilador: IC2.1; also elsewhere on the board
CO: P1.4, R20.1, R23.1, U2.2
GND: R17.2, R18.2, R19.2; also elsewhere on the board
Nac: C4.2, C5.2, C6.2, P1.5, U2.1, U3.1, U4.1
unnamed: C4.1, R23.2
unnamed: C5.1, R24.2
unnamed: C6.1, R25.2
unnamed: IC1.2, R17.1
unnamed: IC1.4, U2.3
unnamed: IC1.6, R20.2
unnamed: IC2.2, R18.1
unnamed: IC2.4, U3.3
unnamed: IC2.6, R21.2
unnamed: IC3.2, R19.1
unnamed: IC3.4, U4.3
unnamed: IC3.6, R22.2
RE: P1.2, R22.1, R25.1, U4.2
VE: P1.3, R21.1, R24.1, U3.2
Vac: P1.1

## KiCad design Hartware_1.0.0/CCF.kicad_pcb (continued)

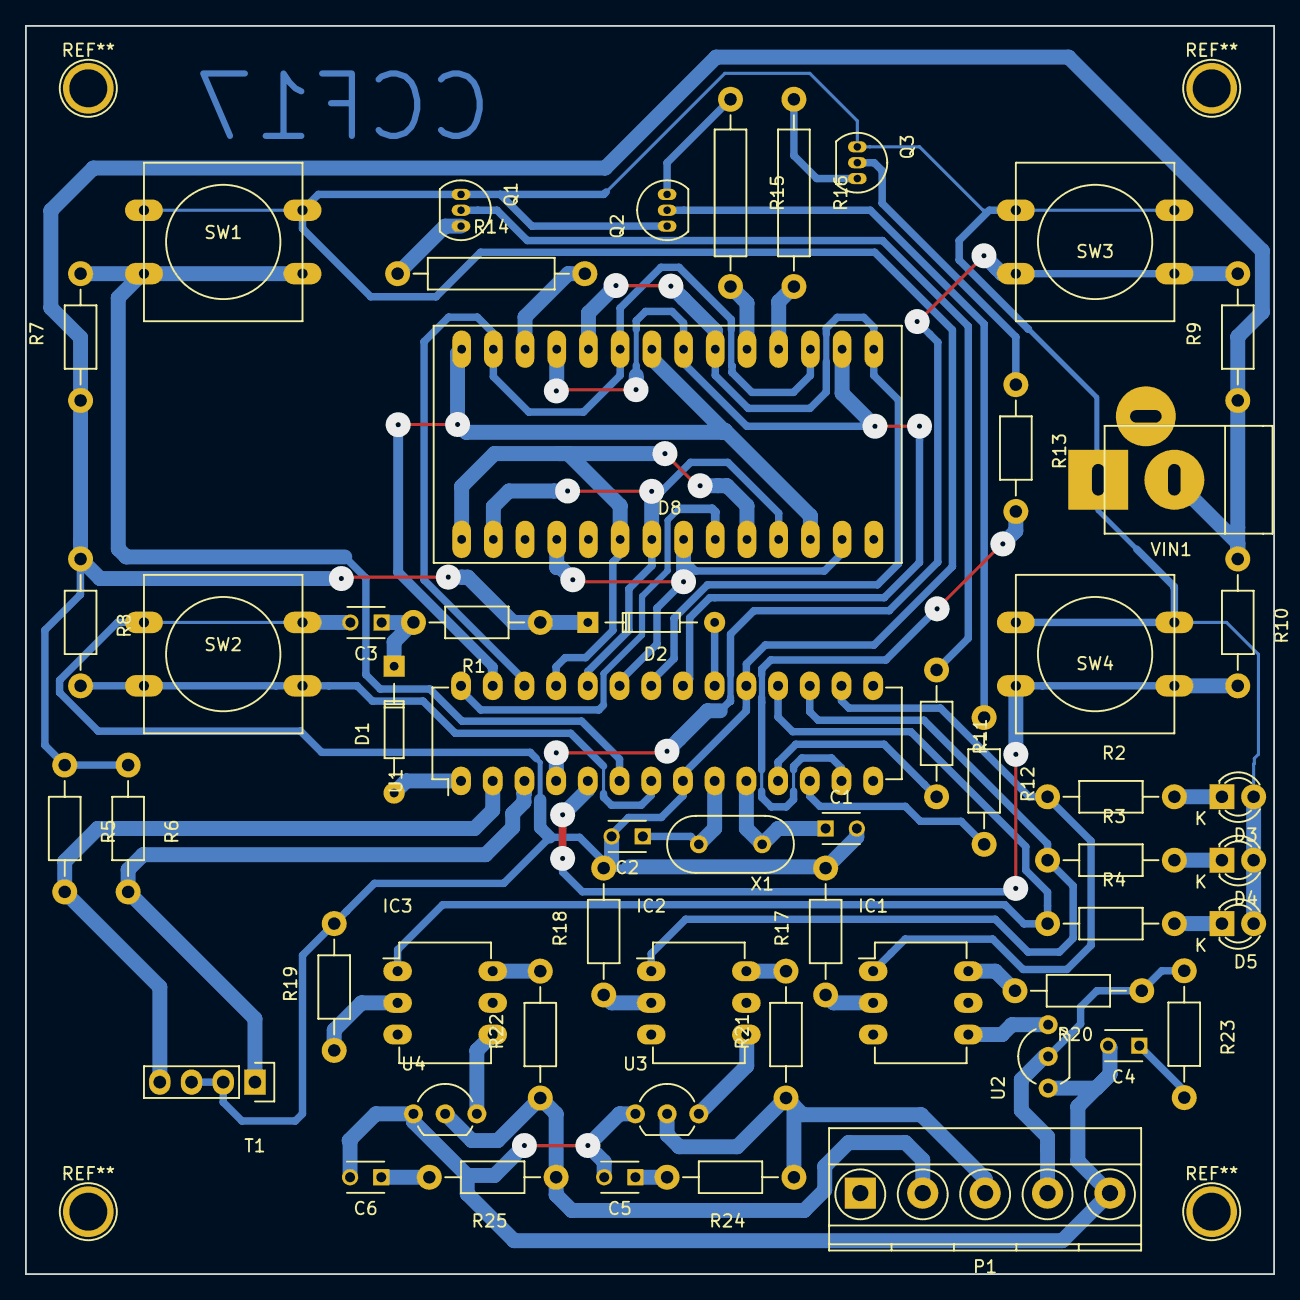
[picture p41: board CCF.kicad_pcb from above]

Board: 2 copper layers, 100.0 x 100.0 mm, 55 parts (0 on the bottom side), 55 nets.

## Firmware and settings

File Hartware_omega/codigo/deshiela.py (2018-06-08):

import math
import onionGpio
import time
import json
import httplib
#from OmegaExpansion import onionI2C

#///////////////////////////////PAQUETES/////////////////////////////////////////
#//CONFIGURACION DEL ARREGLO(Tcomp,Tvent,Tdesc,Fdesc(horas),t_aire,t_refrig,Delta_t)
#//VARIABLES DE CONTROL

gpio15  = onionGpio.OnionGpio(15)#compresor
gpio16  = onionGpio.OnionGpio(16)#Ventilador
gpio17  = onionGpio.OnionGpio(17)#Resistencia
ret1=gpio15.setOutputDirection(0)
ret2=gpio16.setOutputDirection(0)
ret3=gpio17.setOutputDirection(0)
#///////////////VARIABLES PARA TIEMPO////////////////////////////////////////////
segundos = 0
minutos = 0
horas = 0
horas_2 = 0
#/////////////////VARIABLES PARA LEER TEMPERATURA////////////////////////////////
T1 = False
T2 = False
temp1=0
temp2=0
termistor = 0

BAN_1 = 0
BAN_2 = 0
BAN_3 = 0
BAN_C = 0
ERROR = 0

#////////////////VARIABLES PARA LEER VOLTAJE/////////////////////////////////////
def configuracion():
  data = open('setpoint.json','r')
  valores= data.read()
  data.close()
  sp = json.loads(valores)
  return sp
  
#////////////////////////////////////////////////////////////////////////////////
def reloj():
  global segundos
  global minutos
  global horas
  if segundos == 60:
    minutos+=1
    segundos = 0
  elif minutos == 60:
    horas+=1
    horas_2+=1
    minutos = 0
  elif horas == 24:
    horas = 0
#////////////////////////////////////////////////////////////////////////////////

def temperatura():
  DATO=345
  global temp1
  global temp2
  #conn = httplib.HTTPSConnection("api.thingspeak.com")
  #codigo del I2C
  temp1 = convertirTemperatura(DATO)#temperatura refrigerante
  #cap=conn.request("GET", "/update?api_key=9CFTWW3LAB16YBDE&field1="+str(temp1))
  #r1 = conn.getresponse()
  gpio15.setValue(1)#prendo compresor
  """PRENDER LED PARA AVISAR"""
  time.sleep(20.0)
  gpio15.setValue(0)#prendo compresor
  temp2= convertirTemperatura(DATO)
  #cap2=conn.request("GET", "/update?api_key=9CFTWW3LAB16YBDE&field2="+str(temp2))
  #r1 = conn.getresponse() 
  time.sleep(20.0)
  #conn.close()

#////////////////////////////////////////////////////////////////////////////////
def convertirTemperatura(temperaturaBinaria):
  B = 3400.0 #BETA DEL NTC real: B=3400
  Ro = 4700.0 # //RESISTENCIA A 25C
  Rs = 20000.0 #RESISTENCIA DE LINEALIDAD
  Vt = 3.3*temperaturaBinaria/4096 #VOLTAJE DE ENTRADA
  #print "valor del voltaje", Vt
  if Vt==3.3:
    print "El sensor esta en Corto"
    exit()
  elif Vt==0:
    print "El sensor esta en Circuito Abierto"
    exit()
  else:  
    Rt = (Vt*Rs)/(5-Vt) #RESISTENCIA A TEMPERATURA MEDIDA
  T = (1/((math.log(Rt/Ro)*(1/B))+(1/298.15)))-273.15 #TEMPERATURA MEDIDA
  #print "valor de temperatura",T
  return T

#////////////////////////////////////////////////////////////////////////////////
def resetTime():#reseteo tiempos
  segundos = 0
  minutos = 0
  horas = 0
#////////////////////////////////////////////////////////////////////////////////

def comparador(): #compara todos los estados y tiempos
  
  global horas_2
  global BAN_1
  global BAN_2
  global BAN_3
  global BAN_C
  global ERROR
#//////////////// inicio de proteccion  /////////////////////////////////////////
  if minutos >= setPoint["Tcomp"] and BAN_1 == 0 or BAN_C == 1:
    
    gpio15.setValue(1)#prendo compresor
    resetTime() #reseteo tiempo
    BAN_1 = 1
    BAN_C = 0
  if minutos >= setPoint["Tvent"] and BAN_1 == 1:
    if temp1 - setPoint["t_refrig"] < 0 and BAN_1 == 1: #ENCENDIDO POR TEMPERATURA (1)*
      gpio16.setValue(1)#prendo ventilador
      resetTime() #reseteo tiempo
      BAN_1 = 0
#//////////////// fin de proteccion /////////////////////////////////////////////
#////////////inicio de funcion termostato ////////////////////////////////
  if (temp1 - setPoint["t_refrig"]) < setPoint["t_aire"] and BAN_2 == 0:
    gpio15.setValue(0)#apago compresor
    resetTime() #reseteo tiempo
    BAN_2 = 1
  elif minutos == setPoint["t_refrig"] and temp1 + setPoint["t_aire"] > setPoint["t_refrig"] and BAN_C == 0:
    BAN_C = 1
    BAN_2 = 0
#/////////////////// fin de funcion termostato //////////////////////////////////
#////////////////////////inicio de descarche/////////////////////////////////////
  if horas_2 >= setPoint["Tdesc"]: 
    #gpio14.setValue(0)#apago compresor
    #gpio15.setValue(0)#apago ventilador
    #gpio16.setValue(1)#prendo Resistencia
    resetTime() #reseteo tiempo
    horas_2 = 0
    BAN_3 = 1
    BAN_C = 0

  if minutos >= setPoint["Tdesc"] and BAN_3 == 1: 
    #OUTPUT_LOW(RESISTENCIA) ;
    resetTime()
    ERROR = 1 #ERROR EXISTE PORQUE SE APAGA POR RESISTENCIA
    BAN_1 = 0
    BAN_2 = 0
    BAN_3 = 0

  elif temp2 + setPoint["t_refrig"] >= setPoint["t_aire"] and BAN_3 == 1:
    #OUTPUT_LOW(RESISTENCIA) ;
    resetTime()
    BAN_1 = 0
    BAN_2 = 0
    BAN_3 = 0
#///////////////////////FIN DE DESCARCHE/////////////////////////////////////////  
def main():
  global setPoint
  setPoint = configuracion()
  print "Valor de refrigerante: "+str(setPoint["t_refrig"])
  while 1:
    reloj()
    temperatura()
    comparador()
    time.sleep(1.0)
   
if __name__ == '__main__':
  main()

#// (1)*: DEBO ESPERAR HASTA QUE LA TEMPERATURA ESTE POR DEBAJO DE CERO GRADOS Y
#// TAMBIEN HALLA TRANSCURRIDO UN TIEMPO PARA CONSIDERAR QUE EL VENTILADOR NO
#// DISPARARA AIRE CALIENTE AL SISTEMA

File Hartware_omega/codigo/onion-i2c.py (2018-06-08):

from OmegaExpansion import onionI2C
import time
import sys

print 'Starting: onionI2C module testing...'

i2c 	= onionI2C.OnionI2C(0)

# set the verbosity
i2c.setVerbosity(1)

devAddr = 0x68

size 	= 1
addr 	= 0x03
value	= [0x05]
val 	= i2c.writeBytes(devAddr, addr, value)
print '   Set dia semana: ', val


print ""
ret = raw_input('  Ready to read?')

while 1:
	# perform series of reads
	size 	= 1
	addr 	= 0x00
	val 	= i2c.readBytes(devAddr, addr, size)
	print '   Segundos: ', val

	size 	= 1
	addr 	= 0x01
	val 	= i2c.readBytes(devAddr, addr, size)
	print '   Minutos: ', val

	size 	= 1
	addr 	= 0x02
	val 	= i2c.readBytes(devAddr, addr, size)
	print '   Horas: ', val

	size 	= 1
	addr 	= 0x03
	val 	= i2c.readBytes(devAddr, addr, size)
	print '   Dias semana: ', val

	size 	= 1
	addr 	= 0x04
	val 	= i2c.readBytes(devAddr, addr, size)
	print '   Dias: ', val

	size 	= 1
	addr 	= 0x05
	val 	= i2c.readBytes(devAddr, addr, size)
	print '   Mes: ', val

	size 	= 1
	addr 	= 0x06
	val 	= i2c.readBytes(devAddr, addr, size)
	print '   Ano: ', val

	time.sleep(1.0)

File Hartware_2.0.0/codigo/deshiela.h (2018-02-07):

#include <18F2550.h>
#device adc=10

#FUSES NOWDT                    //No Watch Dog Timer
#FUSES WDT128                   //Watch Dog Timer uses 1:128 Postscale
#FUSES PLL1                     //No PLL PreScaler
#FUSES CPUDIV1                  //No System Clock Postscaler
#FUSES NOUSBDIV                 //USB clock source comes from primary oscillator
#FUSES XT                       //Crystal osc <= 4mhz for PCM/PCH , 3mhz to 10 mhz for PCD
#FUSES NOFCMEN                  //Fail-safe clock monitor disabled
#FUSES NOBROWNOUT               //No brownout reset
#FUSES NOLVP                    //No low voltage prgming, B3(PIC16) or B5(PIC18) used for I/O
#FUSES NOXINST                  //Extended set extension and Indexed Addressing mode disabled (Legacy mode)

///SALIDAS
#DEFINE COMPRESOR       PIN_C5
#DEFINE VENTILADOR      PIN_C6
#DEFINE RESISTENCIA     PIN_C7

///USUARIO
#DEFINE BOTON_PROGRA    PIN_A2
#DEFINE BOTON_SELECT    PIN_A3
#DEFINE BOTON_MAS       PIN_A4
#DEFINE BOTON_MENOS     PIN_A5

#use delay(clock=4000000)

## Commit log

2018-02-07 inicio control de tesis
    [7SEGMENTOS_X_3-2018-02-07-09-56-17.sch, 7SEGMENTOS_X_3-2018-02-07-10-06-36.sch, 7SEGMENTOS_X_3.sch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]
2018-02-08 primer trabajo de codificacion
    [7SEGMENTOS_X_3-2018-02-07-10-06-36.sch, 7SEGMENTOS_X_3.sch, Acon_NTC-2018-02-07-10-06-36.sch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]
2018-02-08 modificacion de cartas
    [Cerebro.sch, D21_2550.csv, D21_2550.kicad_pcb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]
2018-02-12 a medio hacer
    [Botones.sch, Cerebro.sch, D21_2550.csv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]
2018-02-12 final placa v2
    [Botones.sch, Cerebro.sch, D21_2550.kicad_pcb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]
2018-02-13 termino parcial de la version 2
    [7SEGMENTOS_X_3.sch, Acon_NTC.sch, Botones.sch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]
2018-02-13 agregando BOM
    [Cerebro.sch, D21_2550.csv, D21_2550.kicad_pcb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]
2018-02-13 creando archivo step
    [D21_2550.kicad_pcb]
2018-02-18 agregando archivos finales
    [D21_2550-B.Adhes.gbr, D21_2550-B.CrtYd.gbr, D21_2550-B.Cu.gbr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]
2018-02-18 finalinzando la placa
    [Acon_NTC.sch, D21_2550.kicad_pcb, FuenteST.sch]
2018-02-19 colocando conector de JST de 90grados
    [Acon_NTC.sch, D21_2550.kicad_pcb]
2018-03-02 lista por hacer
    [Cerebro.sch, D21_2550.kicad_pcb, OutTriac.sch]
2018-03-15 agregando carta de le empresa y modificando tomo
2018-03-15 modificando carta de la empresa
2018-04-14 agregando omega
    [FuenteST.sch, OutTriac.sch, omega-dock-new.kicad_pcb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]
2018-04-14 agregando modelo 3d
    [FuenteST.sch, omega-dock-new.kicad_pcb, omega-dock-new.sch]
2018-04-14 agregando stp
    [omega-dock-new.kicad_pcb]
2018-04-26 culminando hartware omega 2
    [FuenteST.sch, OutTriac.sch, omega-dock-new.csv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]
2018-06-08 pasandome a mac
    [D21_2550.csv, D21_2550.kicad_pcb, FuenteST.sch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]
